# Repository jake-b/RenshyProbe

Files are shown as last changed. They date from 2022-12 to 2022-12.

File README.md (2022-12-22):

# RenshyProbe
A touch probe based on the [Klicky](https://github.com/jlas1/Klicky-Probe) dock system.

**DO NOT MAKE ONE OF THESE** - It's not ready for prime time.  It doesn't work right.  It may never work right.  I am posting this here just to solicit ideas and comments.

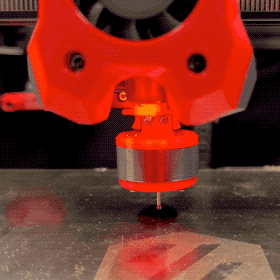
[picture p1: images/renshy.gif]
Renshy Probe

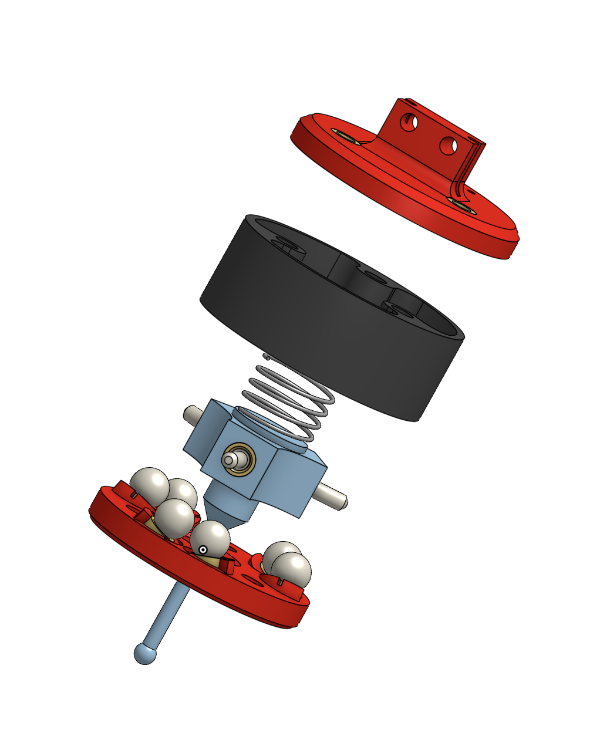
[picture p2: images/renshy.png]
Renshy Probe CAD


# Bill of Materials

- Printed Parts
- M3 threaded inserts
- 5.5mm steel ball bearings
- Probe tip (https://www.aliexpress.us/item/3256802864707715.html)
- M2.5 threaded insert (for probe tip)
- Spring (still figuring out which is best)
- Pins M3x10.3 (https://www.aliexpress.us/item/2255800449635546.html)
- M3 screws to hold it together
- Klicky Probe parts, magnets and screws
- A bit of 22AWG solid wire (stripped)

# Building it

- Print the parts
- Cut some wire
- Sink the M3 inserts into the 6 places that serve as the seat for the ball bearings. Insert a bit of the 22AWG wire between the insert and the printed plastic part before you press in the insert.  When you're done you should have a circuit with breaks where the balls go, and two leads that lead up to the Klicky dock mount.  Note these go in at an angle.
- For the hub, press in the inserts and thread in the pins.  Press in a 2.5mm heat set insert and install the probe.
- Place the balls carefully in their seats.
- Try to close it all up with the spring in place, and the wires leading up and out
- Feel the anger as the balls go everywhere and you fail to do it.
- Try again, and eventually get it together.
- Find that it doesn't yet work.

# What works

- it does dock and undock
- it does trigger (sometimes) in the Z-axis

# What's wrong with it?

- I've found that it triggers on movement.  Maybe need a stiffer spring?
- I've found that it doesn't reliably trigger
- While I have gotten a 5-probe cycle to successfully return a valid result, very often it does not due to "Probe samples exceed tolerance"-- possibly related to the above too issues
- It might need too much lateral force to trigger before pushing off the Klicky magnetic mount.
- The circuit seems high resistance even when closed.  (on the order of 100Ω or so)
- The balls fall out and rattle around inside if you're too rough with it.  Its hard to get them back in place without disassembling it.

# What needs to be done?

- Make it more reliable
- Some Klipper code that allows probing in the X and Y axes, not just the Z-axis.
- Some more code to make it useful for things.
- Experiment with different geometries for the ball seats.  
- Different sized balls
- Different springs

# Why did I want one?

- I've always wanted a 5-way touch probe. 
- It could be used for making point clouds of things (scanning objects)
- It could be used for calibrating the printer automatically (measuring a single perimeter thickness and determining the extrusion multiplier)
- It could be used to find its own nozzle offset by measuring a 3D printed structure that is in a known location on the bed.

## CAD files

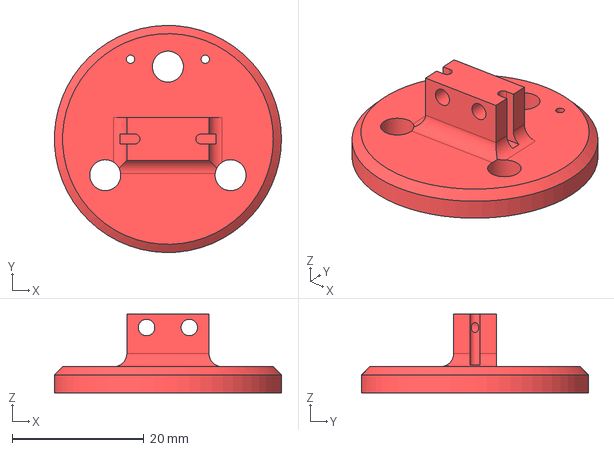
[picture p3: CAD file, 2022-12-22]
CAD/top.step
34.5 x 34.5 x 12.0 mm

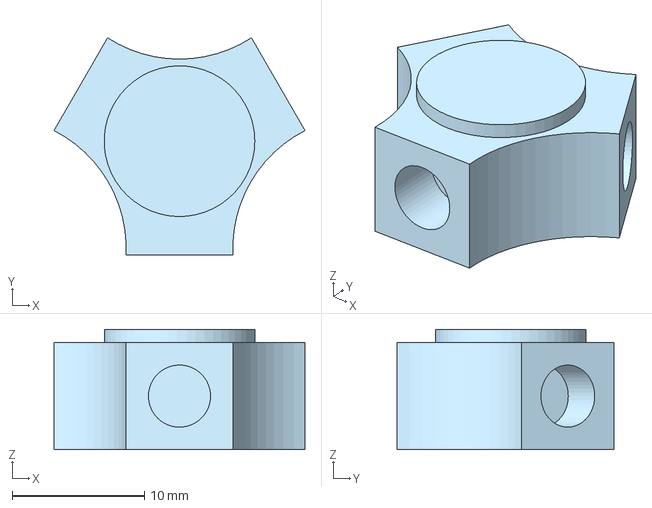
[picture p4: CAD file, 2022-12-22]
CAD/hub.step
19.0 x 16.4 x 9.10 mm

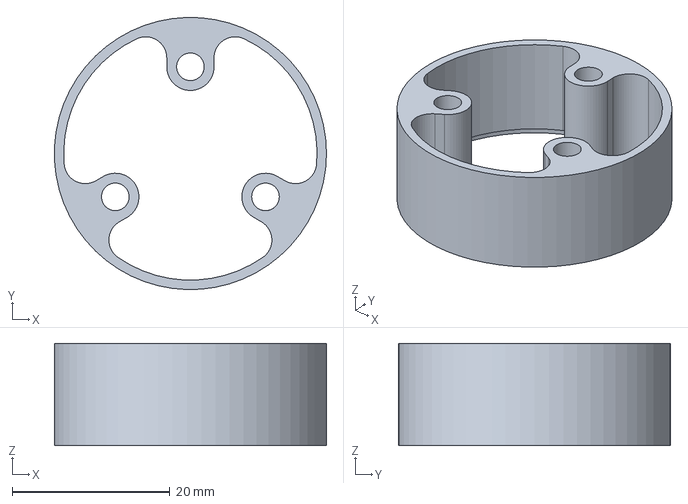
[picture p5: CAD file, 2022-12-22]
CAD/body.step
34.5 x 34.5 x 13.0 mm

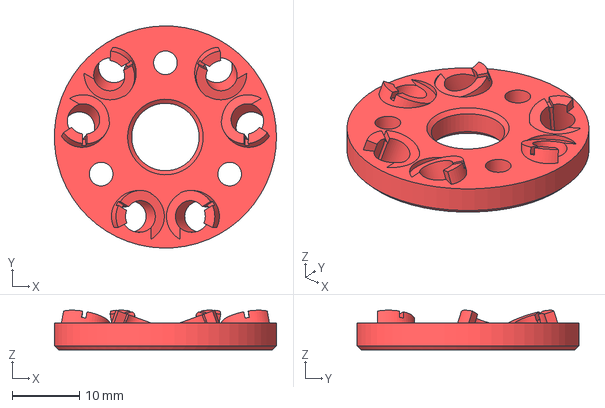
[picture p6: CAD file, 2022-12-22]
CAD/base.step
32.9 x 32.9 x 5.88 mm

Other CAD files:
STLs/base.stl
STLs/body.stl
STLs/hub.stl
STLs/top.stl
